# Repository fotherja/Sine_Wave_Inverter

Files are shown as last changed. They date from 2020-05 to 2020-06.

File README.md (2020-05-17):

# Sine_Wave_Inverter

This software runs on an atmega328p inside a repurposed inverter. The aim of the project was to have an inverter that could power a mini-fridge inside a campervan from a 24v battery. It draws 250uA when the fridge is off. 

Bought inverters have a quiescent power draw due to the DC/DC converter inside them. Even ~6 Watts = 150wh/day which is horrid when you reliant on solar power. I wanted one that could sense when the fridge is off and enter a low power mode. I also wanted a sine wave output for smooth and efficient running. And hey, why not soft start the fridge to reduce the current stresses at startup?

I bought a £30 2nd hand 24v 300w modified sine wave inverter for it's parts and enclosure. I've tapped off the 320v DC it generates and use this to provide a DC rail for a simple H-Bridge circuit on a custom PCB from OSHpark. The Atmega328p generates the PWM signals to drive this H-Bridge that after filtering form a clean sinewave. 

This software is responsible for generating the PWM. It also enables and disables the inverter's DC-DC (24v-320v) converter which is responsible for most of the quiescent current draw. It monitors the DC input current measured by the ACS712 hall effect sensor to know whether the inverter is powering anything or not and enter a low power mode accordingly. Voltage sensing prevents overdischarge of the battery.

Pin descriptions are clearly defined in the software.

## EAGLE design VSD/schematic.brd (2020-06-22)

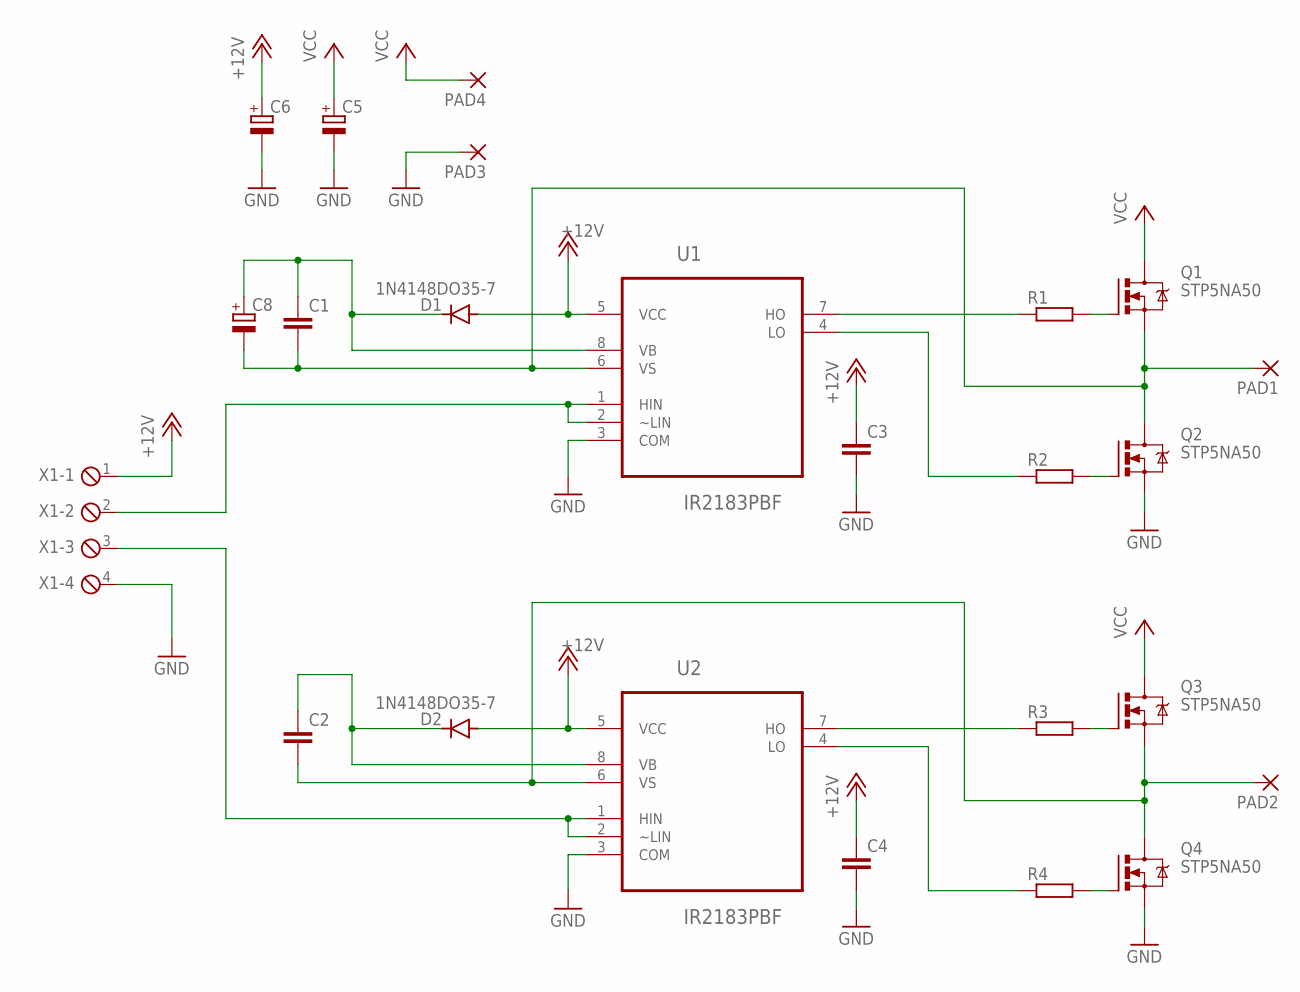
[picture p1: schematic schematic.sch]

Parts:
C1, C2, C3, C4: C-EU050-024X044; C050-024X044
C5: CPOL-EUE5-10.5; E5-10,5
C6, C8: CPOL-EUE2.5-6; E2,5-6
D1, D2: 1N4148DO35-7; DO35-7
PAD1, PAD2, PAD3, PAD4: 3,81/1,4
Q1, Q2, Q3, Q4: STP5NA50; TO220BV
R1, R2, R3, R4: R-EU_0204/7; 0204/7
U1, U2: IR2183PBF; DIP254P762X533-8
X1: MPT4; 4POL254

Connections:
+12V: C3.1, C4.1, C6.+, D1.A, D2.A, U1.5 (VCC), U2.5 (VCC), X1.1
GND: C3.2, C4.2, C5.-, C6.-, PAD3.1, Q2.S, Q4.S, U1.3 (COM), U2.3 (COM), X1.4
unnamed: Q2.G, R2.2
unnamed: C1.2, C8.-, PAD1.1, Q1.S, Q2.D, U1.6 (VS)
unnamed: Q1.G, R1.2
unnamed: R1.1, U1.7 (HO)
unnamed: R2.1, U1.4 (LO)
unnamed: C1.1, C8.+, D1.C, U1.8 (VB)
unnamed: U1.1 (HIN), U1.2 (~LIN), X1.2
unnamed: Q4.G, R4.2
unnamed: C2.2, PAD2.1, Q3.S, Q4.D, U2.6 (VS)
unnamed: Q3.G, R3.2
unnamed: R3.1, U2.7 (HO)
unnamed: R4.1, U2.4 (LO)
unnamed: C2.1, D2.C, U2.8 (VB)
unnamed: U2.1 (HIN), U2.2 (~LIN), X1.3
VCC: C5.+, PAD4.1, Q1.D, Q3.D

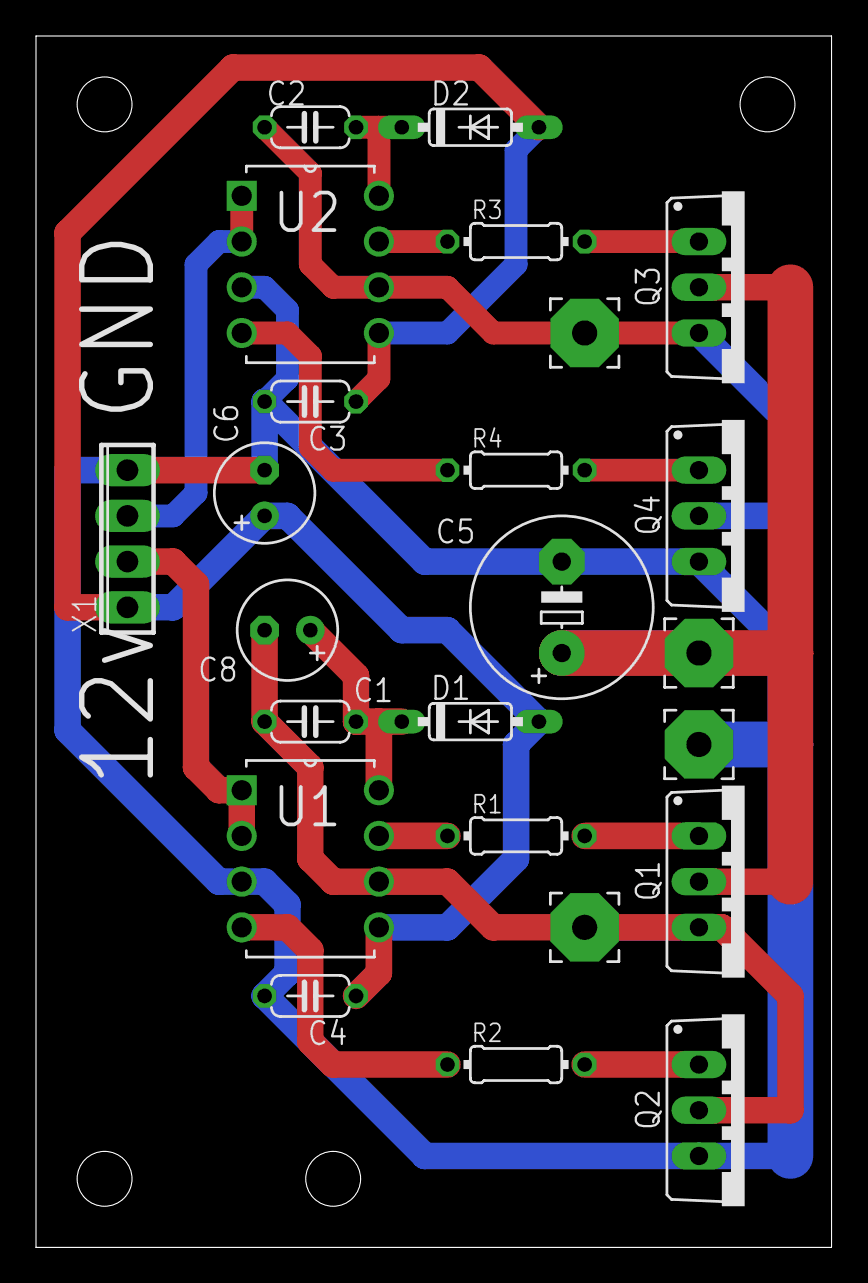
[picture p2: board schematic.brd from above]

Board: 2 copper layers, 44.2 x 67.3 mm, 24 parts (0 on the bottom side), 17 nets.

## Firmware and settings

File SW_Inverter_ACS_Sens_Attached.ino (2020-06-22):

/*
  J.Fotherby 2020  
  Sinewave inverter: Amplitude and frequency adjustable, current detection 

  // Depending on whether the ACS current sensor is attached we behave differently
    DETACHED - Soft start and stay on continuously
    ATTACHED - Perform as below

  1) Do nothing for 5 minute after turn on -> to allow compressor pressures to equalise (should device be turned off and then straight on again)
  2) Enable the inverter and pause for 2 seconds (Allows the initial inrush current to die down)
  3) Generate a 30Hz output signal
  4) Measure the ~24v DC input current over the next 1 second (Using the ADS712-5A current sensor) 
  5) If 1 second average <1.0Amps then jump to 7), else start ramping the output from 30 to 50Hz adjusting the amplitude proportionally
  6) Monitor the previous 1 second current and voltage averages, if <1.0Amps OR < 20.0v move to step 7)
  7) Enter low power mode, wait 20 minutes
  8) If input voltage average > 21.0v return to step 2)

  # ADC 0 -> Measures input current
  # ADC 2 -> Measures input voltage

  In order to keep to the 4.6v/Hz that appliances expect the inverter measures the input voltage just before startup. If < AMP_ADJUST_THRES (23.2v):
    A) Limit the max_frequency to MAX_FREQUENCY_LOW (45Hz)
    B) Use a different amplitude adjust lookup table

  This should help the fridge run more efficiently. 
*/
 
//------------------------------------------------------------------------------------- 
//-------------------------------------------------------------------------------------
#include "LowPower.h"

//#define _DEBUG_MODE_                                          // Commenting out this will prevent all Serial port communication
 
#define         CURRENT_SENSE       A0                           
#define         INVERTER_CTRL_PIN   A1                          // This switches the DC-DC converter on/off for power savings
#define         VOLTAGE_SENSE       A2
#define         PHASE_B_PIN         A3                          // Our low frequency phase flipping square wave output

#define         ACS_nENABLE         2                           // When Low, powers the ACS712, When high, shuts it down
#define         LED_PIN             9                           // Just an indicator LED
#define         PHASE_A_PIN         10                          // Our High frequency PWM pin

#define         SINE_STEPS          256                         // Number of steps to build our sinewave in

#define         STATE_OFF           0
#define         STATE_HOLD          1
#define         STATE_RAMP          2
#define         STATE_ON            3 

#define         START_FREQUENCY     42                          // 42 corrosponds to a 30Hz start frequency
#define         MAX_FREQUENCY_HIGH  127                         // Corrosponds to 50Hz
#define         MAX_FREQUENCY_LOW   107                         // Corrosponds to 45Hz
#define         RAMP_TIMESTEP       47                          // Timestep of 47ms corrosponds to a frequency ramp at a rate of ~4.5Hz/sec (also chosen to avoid aliasing of ADCs)
#define         HOLD_TIME           1000                        // Time to stay at the startup frequency to check if fridge connected or not.
#define         SHUTDOWN_TIME       (1200000 / 21)              // Try powing up the fridge after 20 minutes from when it shuts off (like this because powerDown stops the timers etc)

#define         LOW_VOLT_CUTOUT     8100                        // When voltage falls below this value we shutdown to protect the battery
#define         LOW_VOLT_CUTIN      8360                        // 8100 - 8360 corrisponds to 21.5v - 22.2v
#define         NO_LOAD_I_THRESHOLD 5600                        // If current is less than this we assume the inverter is not powering anything (< ~1Amp)

#define         AMP_ADJUST_THRES    8760                        // ~23.2v, less than this and we set a max frequency of 45Hz == 107 and adjust our amplitude scaling at startup

void Startup ();
void Shutdown ();
void Detect_ACS ();
void Set_Max_Freq();

//-------------------------------------------------------------------------------------
unsigned int    Sine_Lookup[128]          =       {0,20,39,59,78,98,117,137,156,175,194,213,232,251,269,288,            // Duty cycles to step through to produce a sinewave
                                                  306,324,342,359,377,394,411,427,444,460,476,492,507,522,537,551,
                                                  565,579,592,605,618,630,642,653,664,675,685,695,705,714,722,730,
                                                  738,745,752,759,765,770,775,780,784,787,790,793,795,797,798,799,
                                                  799,799,798,797,795,793,790,787,784,780,775,770,765,759,752,745,
                                                  738,730,722,714,705,695,685,675,664,653,642,630,618,605,592,579,
                                                  565,551,537,522,507,492,476,460,444,427,411,394,377,359,342,324,
                                                  306,288,269,251,232,213,194,175,156,137,117,98,78,59,39,20};

byte            Step_Delay_LOOKUP[128]    =       {195,193,191,189,187,184,182,180,178,177,175,173,171,169,168,166,     // Microsecond delays to produce frequencies from 20 to 50Hz
                                                  164,163,161,160,158,156,155,154,152,151,149,148,147,145,144,143,
                                                  142,141,139,138,137,136,135,134,133,132,131,130,129,128,127,126,
                                                  125,124,123,122,121,120,119,118,118,117,116,115,114,114,113,112,
                                                  111,110,110,109,108,108,107,106,106,105,104,104,103,102,102,101,
                                                  100,100,99,99,98,97,97,96,96,95,95,94,94,93,93,92,
                                                  92,91,91,90,90,89,89,88,88,87,87,86,86,85,85,85,
                                                  84,84,83,83,82,82,82,81,81,80,80,80,79,79,78,78};

byte            Amp_Freq_Adj_LOOKUP_HIGH[128]  =  {26,26,26,27,27,27,27,28,28,28,29,29,29,30,30,30,                     // Multiplication factors (>23.5)
                                                  30,31,31,31,32,32,32,33,33,33,33,34,34,34,35,35,
                                                  35,36,36,36,36,37,37,37,38,38,38,39,39,39,40,40,
                                                  40,40,41,41,41,42,42,42,43,43,43,43,44,44,44,45,
                                                  45,45,46,46,46,46,47,47,47,48,48,48,49,49,49,49,
                                                  50,50,50,51,51,51,52,52,52,53,53,53,53,54,54,54,
                                                  55,55,55,56,56,56,56,57,57,57,58,58,58,59,59,59,
                                                  59,60,60,60,61,61,61,62,62,62,62,63,63,63,64,64};

byte            Amp_Freq_Adj_LOOKUP_LOW[108]  =   {28,29,29,29,30,30,30,31,31,31,32,32,32,33,33,33,                     // Multiplication factors (<23.5)
                                                  34,34,34,35,35,35,36,36,37,37,37,38,38,38,39,39,
                                                  39,40,40,40,41,41,41,42,42,42,43,43,43,44,44,44,
                                                  45,45,45,46,46,46,47,47,47,48,48,48,49,49,49,50,
                                                  50,50,51,51,51,52,52,52,53,53,53,54,54,54,55,55,
                                                  55,56,56,56,57,57,57,58,58,58,59,59,59,60,60,60,
                                                  61,61,61,62,62,62,63,63,63,64,64,64};
            
int             Index_Phase         = 0;                        // Index incremented to step through the sinewave generation duty cycles
byte            Amplitude_Adj       = 32;                       // We multiply the duty cycle value by this then >> 6 (ie. /64) It's a CPU efficient way of scaling values 
byte            Step_Delay_us       = 125;                      
byte            State               = STATE_OFF;                // Either OFF, HOLD, RAMP or ON            
byte            ACS_Attached_YN     = 0;        
byte            Frequency           = START_FREQUENCY;          // This is not in hertz. The range is 0-127 which corrosponds to 20-50Hz
byte            Frequency_Limit     = MAX_FREQUENCY_HIGH;

unsigned long   TimeStamp_Sine      = 0;
unsigned long   TimeStamp_Ramp      = 0;
unsigned long   TimeStamp_Startup   = 0;
unsigned long   TimeStamp_Shutdown  = millis() - 42857;         // Trick into thinking we shut down 15 minutes ago so we only wait 5 minutes before trying a start up [42857]

//-------------------------------------------------------------------------------------
void setup() 
{  
  digitalWrite(INVERTER_CTRL_PIN, LOW);  
  digitalWrite(ACS_nENABLE, HIGH);    
  digitalWrite(PHASE_A_PIN, LOW);    
  digitalWrite(PHASE_B_PIN, LOW); 
  digitalWrite(LED_PIN, LOW);

  pinMode(INVERTER_CTRL_PIN, OUTPUT);
  pinMode(ACS_nENABLE, OUTPUT);       
  pinMode(PHASE_A_PIN, OUTPUT);   
  pinMode(PHASE_B_PIN, OUTPUT);
  pinMode(LED_PIN, OUTPUT);
  
  TCCR1A = 0b00100010;
  TCCR1B = 0b00011001;                                          // Configure for 20KHz FAST PWM with ICR1 control
  ICR1 = 799;
  TCNT1 = 0; 
  OCR1B = 0;

  ADMUX = B01000000;                                            // Turn on ADC
  ADCSRA = B10000111;                                           // 128 Prescaler -> ADC Clk = 125KHz
  ADCSRA |= B01000000;                                          // Start a conversion in the background

  #ifdef _DEBUG_MODE_
    Serial.begin(115200);
    Serial.println("Performing ACS detection:");
  #endif
  
  delay(100);
  Detect_ACS();                                                 // Sets ACS_Attached_YN = 0 if not attached and 1 if attached
}

//-------------------------------------------------------------------------------------
void loop() 
{      
  if(millis() - TimeStamp_Ramp >= RAMP_TIMESTEP)                // Periodic function runs every RAMP_TIMESTEP milliseconds      
  {    
    TimeStamp_Ramp = millis();

    // #########################################################################################################################################
    // 1) Read the ADCs for input voltage and current. Keep 10 value running averages of both stored as SumV and SumI respectively
    static byte indexV = 0, indexI = 0;
    static int BufferV[10], BufferI[10];
    static int SumV, SumI;
    
    if(ADCSRA & B00010000)  {                                   // If ADC conversion complete 
      if(ADMUX == B01000010) {                                  // ADC2 conversion complete
        BufferV[indexV++] = ADCW;                               // Insert latest reading into Buffer and increment index
        if (indexV > 9) {                                       // Keep index within limits
          indexV = 0;
        }
        
        SumV = 0;                                               // Reset Sum
        for(byte i = 0; i < 10; i++)  {                         // Add up all values in buffer
          SumV += BufferV[i];
        }
        
        ADMUX = B01000000;                                      // Select ADC channel 0 this time       
        ADCSRA |= B00010000;                                    // This clears the ADC complete flag and allows the new MUX channel to be written
        ADCSRA |= B01000000;                                    // Start a conversion in the background          
      }
      
      else if(ADMUX == B01000000)  {                            // ADC0 conversion complete
        BufferI[indexI++] = ADCW;                               // Insert latest reading into Buffer and increment index
        if (indexI > 9) {                                       // Keep index within limits
          indexI = 0;
        }
        
        SumI = 0;                                               // Reset Sum
        for(byte i = 0; i < 10; i++)  {                         // Add up all values in buffer
          SumI += BufferI[i];
        }
                          
        ADMUX = B01000010;                                      // Select ADC channel 2    
        ADCSRA |= B00010000;
        ADCSRA |= B01000000;                                    // Start a conversion in the background  
      }
    }      

    // #########################################################################################################################################
    // 2) State logic 
    if(ACS_Attached_YN) {                                       // If ACS712 is attached do this logic:
      if(State == STATE_ON) {                               
        if(SumI < NO_LOAD_I_THRESHOLD)  {                       // If no current is being drawn despite producing an output waveform, we shutdown
          Shutdown();
          #ifdef _DEBUG_MODE_        
            Serial.print("Low current! I: "); Serial.println(SumI);
          #endif 
        }    
        else if(SumV < LOW_VOLT_CUTOUT)  {                      // If the voltage has fallen too low then shutdown        
          Shutdown(); 
          #ifdef _DEBUG_MODE_        
            Serial.print("Undervoltage! V: "); Serial.println(SumV);
          #endif                  
        }        
      }
      else if(Frequency == Frequency_Limit) {                                            
        State = STATE_ON;
      }    
      else if(State == STATE_RAMP) {                            // If we're in the soft start stage increment our frequency if we're not at our limit yet
        Frequency++;
      } 
      else if(State == STATE_HOLD)  {
        if(millis() - TimeStamp_Startup > HOLD_TIME) {          // If we've been producing our 30Hz output for 1 second we'll have a good current draw average measurement
          if(SumI > NO_LOAD_I_THRESHOLD)  {                     // If there is current being drawn the fridge must be connected
            State = STATE_RAMP;                                 // So ramp up the frequency to power the fridge properly
          }
          else  {
            Shutdown();                                         // Otherwise shutdown for a further 20 minutes before trying again
            #ifdef _DEBUG_MODE_        
              Serial.print("Current draw test failed! I: "); Serial.println(SumI);
            #endif 
          }
        }
      }
      else if(State == STATE_OFF)  {
        delay(45);                              
        LowPower.powerDown(SLEEP_1S, ADC_ON, BOD_ON);           // millis() doesn't count during this period! We must alter our SHUTDOWN_TIME define to account for it
        delay(5);
  
        #ifdef _DEBUG_MODE_        
          Serial.print("V: "); Serial.println(SumV);
          Serial.print("I: "); Serial.println(SumI);
          Serial.print("SD Time: "); Serial.println((millis() - TimeStamp_Shutdown)/48); Serial.println();
        #endif
  
        if(SumV > LOW_VOLT_CUTIN) {                             // If our battery voltage is good
          if(millis() - TimeStamp_Shutdown > SHUTDOWN_TIME) {   // And we've completed our [20] minute shutdown period
            Set_Max_Freq(SumV);                                 // Depending on the inverter input voltage, decide what our max fequency can be.
            Startup();                                          // Then try a startup procedure
          }
        }
      }      
    }
    
    else  {                                                     // If ACS NOT attached do this logic
      if(State == STATE_ON) {
        if(SumV < LOW_VOLT_CUTOUT)  {                                  
          Shutdown();   
          #ifdef _DEBUG_MODE_        
            Serial.print("Undervoltage! V: "); Serial.println(SumV);
          #endif     
        }  
      }
      else if(Frequency == MAX_FREQUENCY_HIGH) {                // Without ACS attached, we just run at max voltage and frequency            
        State = STATE_ON;
      }    
      else if(State == STATE_RAMP) {
        Frequency++;
      } 
      else if(State == STATE_HOLD)  {
        State = STATE_RAMP;
      }
      else if(State == STATE_OFF)  {
        delay(45);                              
        LowPower.powerDown(SLEEP_1S, ADC_ON, BOD_ON); 
        delay(5);
  
        #ifdef _DEBUG_MODE_        
          Serial.print("V: "); Serial.println(SumV);
        #endif
  
        if(SumV > LOW_VOLT_CUTIN) {                             // If our battery voltage is good
          Startup();                                            // Then Startup
        }
      }      
    }

    // #########################################################################################################################################
    // 3) Write delay and amplitute values from lookup tables
    Step_Delay_us = Step_Delay_LOOKUP[Frequency];               // Step_Delay_us -> 20Hz - 50Hz 

    if(Frequency_Limit == MAX_FREQUENCY_HIGH) 
      Amplitude_Adj = Amp_Freq_Adj_LOOKUP_HIGH[Frequency];      // Change the amplitude proportional to the frequency. At 25Hz the amplitude should be half that of 50Hz
    else
      Amplitude_Adj = Amp_Freq_Adj_LOOKUP_LOW[Frequency];                    
  }
  
  
  // Vary the duty cycle on PHASE_A. PHASE_B is a square wave. Simultaneously flip our PHASE_A & B lines at the zero crossing points (0 & 180 degrees)
  static unsigned int Next_OCR1B = 0;                           // Allows us to precalculate the OCR1A value for a snappy switch
  if(State != STATE_OFF)
  {
    // Have a constant delay in our loop for stepping through our sinewave generation
    while(micros() - TimeStamp_Sine < Step_Delay_us) {}      
    TimeStamp_Sine += Step_Delay_us; 
    
    // Sinewave generation logic
    if(Index_Phase == 0)  {         
      TCNT1 = 793;                                              // Allow a few clock cycles to complete the following code so PHASE_A & PHASE_B go low simultaneously.              
      OCR1B = 0;    
      PORTC = PORTC & 0b11110111;                               // ie. digitalWrite(PHASE_B, LOW);
      Next_OCR1B = (20 * Amplitude_Adj) >> 6;                   // The index will be 1 next which corrosponds to a lookup value of 20
    }
    else if(Index_Phase < 128)  {
      OCR1B = Next_OCR1B;                                       // We can immediately write to this register because we pre-calculated its value
      Next_OCR1B = (Sine_Lookup[Index_Phase + 1] * Amplitude_Adj) >> 6;
    }    
    else if(Index_Phase == 128) {         
      TCNT1 = 793;                                              // Allow a few clock cycles to complete the following code so PHASE_A & PHASE_B go high simultaneously.  
      OCR1B = 799;  
      PORTC = PORTC | 0b00001000;                               // ie. digitalWrite(PHASE_B, HIGH);
      Next_OCR1B = 799 - ((20 * Amplitude_Adj) >> 6);                          
    }
    else  {
      OCR1B = Next_OCR1B;
      Next_OCR1B = 799 - ((Sine_Lookup[Index_Phase - 127] * Amplitude_Adj) >> 6);
    }

    // Increment the step counter
    Index_Phase += 1;
    if(Index_Phase >= SINE_STEPS)  {
      Index_Phase = 0;
    }  
  }
}

// #########################################################################################################################################
// -------------------------------------------------------  SUB-ROUTINES -------------------------------------------------------------------
// #########################################################################################################################################
void Startup ()
{
  // Startup procedure: Turn the inverter on, then start sinewave generation    
  digitalWrite(INVERTER_CTRL_PIN, HIGH);
  digitalWrite(ACS_nENABLE, LOW);
  digitalWrite(LED_PIN, HIGH);
  delay(2000);

  #ifdef _DEBUG_MODE_        
    Serial.println("Startup!");
  #endif  

  Index_Phase = 0; 
  State = STATE_HOLD;
  Frequency = START_FREQUENCY;
  TimeStamp_Startup = millis(); 
  TimeStamp_Sine = micros();   
}

void Shutdown ()
{
  // Shutdown procedure: Turn off the inverter, then ensure Phase A&B both go low simultaneously 
  digitalWrite(INVERTER_CTRL_PIN, LOW); 
  digitalWrite(ACS_nENABLE, HIGH);  
  digitalWrite(LED_PIN, LOW);

  #ifdef _DEBUG_MODE_        
    Serial.println("Shutdown!");
  #endif 

  State = STATE_OFF; 
  Frequency = START_FREQUENCY;     
  TCNT1 = 793;                                                          
  OCR1B = 0;    
  PORTC = PORTC & 0b11110111;  
  TimeStamp_Shutdown = millis();
}
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

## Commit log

2020-01-09 Initial upload
    Bugs:
    - Glitches in waveform
    - ADC slow and no interrupts yet.
2020-01-12 Amplitude changes with Freq
    Further testing. Eventually have one ADC channel measuring the thermistor and the other measuring the input voltage
2020-03-24 Soft_start working
    Yet to do
    - Voltage compensation
    - Load detection and power down
2020-03-25 Thermistor_Controlled_Full
    Full code for thermistor temperature controlled fridge.
    - Needs full hardware testing for temperature hold and voltage cutout/cutin etc
2020-04-26 Uses ACS712 current sensor
    A good solution. Uses the ACS712 on the 24v input to work out whether a load is connected or not by sensing the current draw on power up. If the fridge switches off this is also detected.
    Logic as follows:
    1) Do nothing for 5 minute after turn on -> to allow compressor pressures to equalise (should device be turned off and then straight on again)
    2) Enable the inverter and pause for 2 seconds (Allows the initial inrush current to die down)
    3) Generate a 30Hz output signal
    4) Measure the 24v input current over the next 1 second (Using the ADS712-5A current sensor)
    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
2020-06-22 Detect ACS712 & limit to 45Hz if low input voltage
    If ACS712 not detected, runs as a normal sine wave inverter (with an initial soft start)
    Detects voltage just before startup. If low limit our max frequency to 45Hz to comply with correct volts/Hz
    [SW_Inverter_ACS_Sens_Attached.ino]
2020-06-22 Added Eagle files for the high voltage H-Bridge
    I built the arduino board housing the voltage regulator, XO, transistor switch to turn the inverter on/off and ADC for input voltage on breadboard. Wish I hadn't.
    [schematic.brd, schematic.sch]
